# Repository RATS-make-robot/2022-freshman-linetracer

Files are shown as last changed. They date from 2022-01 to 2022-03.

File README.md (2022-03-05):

# 2022-freshman-linetracer

2022 신입생 라인트레이서  

## INTRO
- 신입회원은 가입 후 신입생 세미나(C언어, 라인트레이서 제작)을 거치게 됩니다.   
- 세미나에 적극적으로 참여하고 라인트레이서 완성시, 준회원에서 정회원으로 승급됩니다.  
- 정회원이 되어야 RATS에서 계속 활동할 수 있습니다. 

## 작동 영상
ezgif-1-091fc016d1

## Arduino
  - 아두이노 나노 사용
  - 예제 파일 올려둠
    - LED
    - MOTOR
    - SENSOR
## Modeling
  - `Solidworks 2020`으로 설계
  - `몸체`와 `몸체2`를 3D 프린터로 출력 후 조립

## Reference
  - 사용 부품의 데이터 시트 모음

## Schematic
  - `KiCAD`로 회로도 작성

## 부품리스트

[부품리스트 (가격과 판매처 링크가 포함된 버전)](https://mokhwasomssi.notion.site/bc81dec099644cce938beb7883b7c5f4)
- 소자
    |부품|종류|용도|
    |---|---|---|
    |아두이노 나노 호환보드|MCU|라트 개발보드|  
    |스위치|스위치|라트 전원 스위치|
    |7805|레귤레이터|전원부 레귤레이터|
    |캐패시터 0.33uF|캐패시터|전원부 캐패시터|
    |캐패시터 0.1uF|캐패시터|전원부 캐패시터|
    |저항 330Ω|저항|LED 저항|
    |저항 1MΩ|저항|수광 소자 저항|
    |저항 220Ω|저항|발광 소자 저항|
    |LED|LED|전원부 출력 확인, 센서 값 확인|
    |ST5811|발광 소자|주행선 감지|
    |SI5312-H|수광 소자|주행선 감지|

- 모터, 배터리
  |부품|종류|용도|
  |---|---|---|
  |아두이노 RC카 모터|모터|모터|
  |아두이노 RC카 바퀴|바퀴|바퀴|
  |배터리 18650 1200mAh|배터리|리튬 이온 배터리, 충전 가능|
  |배터리 홀더|배터리|18650x2 홀더|

- 소켓, 커넥터, 점퍼
  |부품|종류|용도|
  |---|---|---|
  |핀헤더|소켓|12핀 : 센서 전원, 신호  </br> 8핀 : 모터 전원, 신호|
  |핀헤더소켓|소켓|30핀 : 아두이노</br>3핀 : 레귤레이터|
  |몰렉스 커넥터 - M|커넥터|전원 커넥터|
  |몰렉스 커넥터 - F|커넥터|전원 커넥터|
  |소켓 점퍼 케이블 - F/F|점퍼|센서 전원 및 신호</br>모터드라이버 신호|
  |소켓 점퍼 케이블 - M/F|점퍼|모터드라이버 전원</br>모터 전선|

- 조립
  |부품|종류|용도|
  |----|---|---|
  |부품 수납 케이스|공구함|개인 부품 보관|
  |만능기판 100X100|만능기판|메인보드 납땜|
  |만능기판 100X50|만능기판|센서보드 납땜|
  |서포트 40mm|서포트|메인보드 서포트|
  |서포트 10mm|서포트|모터드라이버 서포트|
  |볼트 M3x10|볼트|메인보드 서포트 고정</br>모터드라이버 서포트 고정</br>볼캐스터 고정</br>센서보드 고정|
  |볼트 M3x16|볼트|몸체-몸체2 조립|
  |볼트 M3x30|볼트|모터 고정|
  |너트 M3|너트|너트|
  |볼캐스터 5/8|볼캐스터|마찰 방지|
  |십자 드라이버 3mm|드라이버|라트 조립|
    
## NOTE
- 배터리 전선에 몰렉스 커넥터 달아야 함
  - 클램프 필수
- 배터리 홀더에 18650 잘 안들어감
  - 꾸겨넣으세요
- 5V랑 ADC 출력 부분이 플럭스로 이어져있으면 ADC 값이 잘 안 받아짐
  - 이유는 잘 모르겠고 경험적으로

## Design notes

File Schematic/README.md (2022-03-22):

# Schematic


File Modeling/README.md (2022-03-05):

# Modeling 

- 제작할 라인트레이서를 3D 모델링 하였습니다.   
- 3D 프린터로 출력해야하는 파트는 `몸체`와 `몸체2`입니다. 
- 출력 파트의 STL 파일, G-code 파일도 업로드 하였습니다. 





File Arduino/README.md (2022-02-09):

# Arduino

## 아두이노 나노 Upload 세팅


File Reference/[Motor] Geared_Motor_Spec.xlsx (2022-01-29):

MODEL | VOLTAGE |  | NO LOAD |  | AT MAXIMUM EFFICIENCY |  |  |  |  | STALL
 | OPERATING RANGE | NOMINA | SPEED | CURRENT | SPEED | CURRENT | TORQUE |  | OUTPUT | TORQUE |  | CURRENT
 |  | V | r/min | A | r/min | A | N.m | Kg.cm | w | N.m | Kg.cm | A
NP02D-288 | 3.0 - 12.0 | 6 | 21 | 0.1 | 19 | 0.17 | 0.05 | 0.47 | 0.18 | 0.18 | 1.8 | 0.6
MODEL | VOLTAGE |  | NO LOAD |  | AT MAXIMUM EFFICIENCY |  |  |  |  | STALL
 | OPERATING RANGE | NOMINA | SPEED | CURRENT | SPEED | CURRENT | TORQUE |  | OUTPUT | TORQUE |  | CURRENT
 |  | V | r/min | A | r/min | A | N.m | Kg.cm | w | N.m | Kg.cm | A
NP01S-220 | 3.0 - 6.0 | 3 | 50 | 0.25 | 34 | 0.45 | 0.07 | 0.71 | 0.52 | 0.24 | 2.4 | 1.1
MODEL | VOLTAGE |  | NO LOAD |  | AT MAXIMUM EFFICIENCY |  |  |  |  | STALL
 | OPERATING RANGE | NOMINA | SPEED | CURRENT | SPEED | CURRENT | TORQUE |  | OUTPUT | TORQUE |  | CURRENT
 |  | V | r/min | A | r/min | A | N.m | Kg.cm | w | N.m | Kg.cm | A
NP01D-48 | 3.0 - 9.0 | 3 | 110 | 0.12 | 85 | 0.2 | 0.01 | 0.11 | 0.13 | 0.027 | 0.27 | 1.45

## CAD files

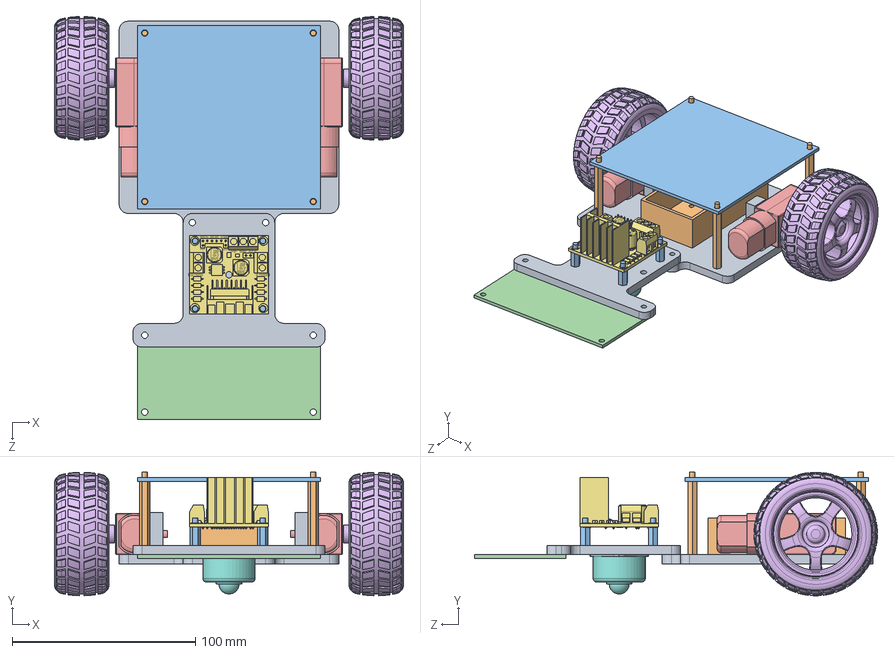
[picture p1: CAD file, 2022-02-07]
Modeling/Modeling Files/조립.SLDASM
190.8 x 67.5 x 220.0 mm
몸체
배터리홀더
메인보드 100x100
센서보드 50x100
모터 x 2
바퀴 x 2
모터드라이버
볼캐스터
몸체2
서포트 M3x40 x 4
서포트 M3x10 x 4

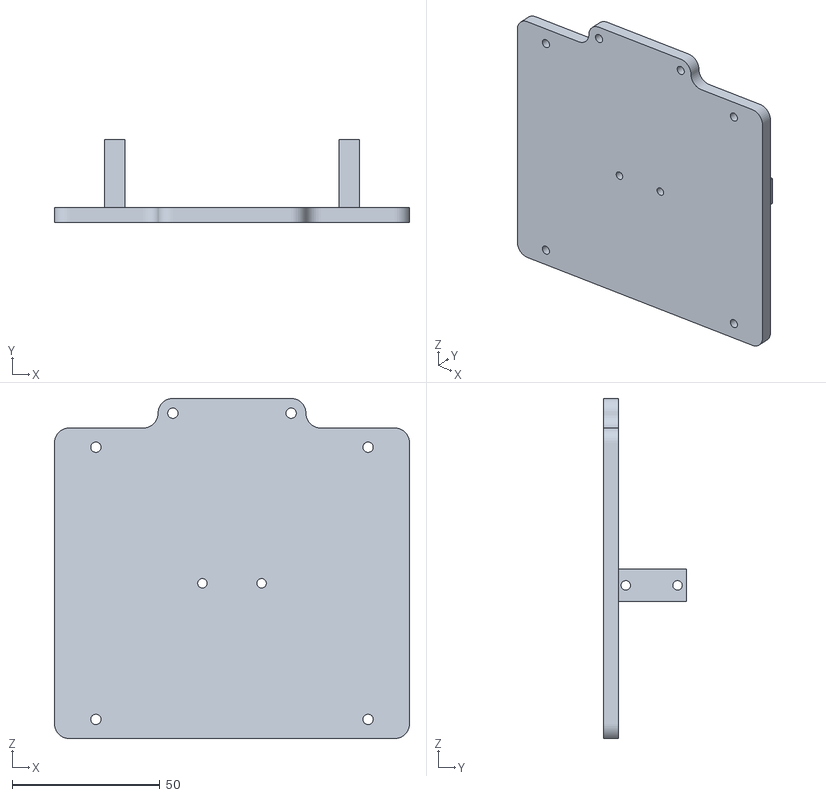
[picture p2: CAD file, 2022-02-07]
Modeling/[출력] 몸체.STL
120.0 x 28.0 x 115.0

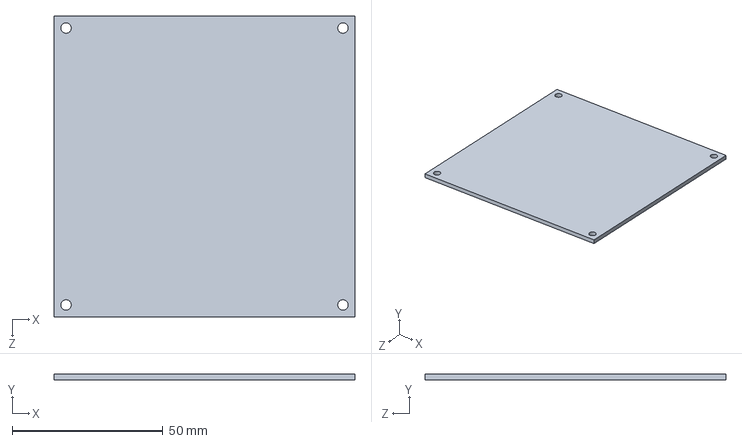
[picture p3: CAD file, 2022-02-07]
Modeling/Modeling Files/메인보드 100x100.SLDPRT
100.0 x 2.00 x 100.0 mm

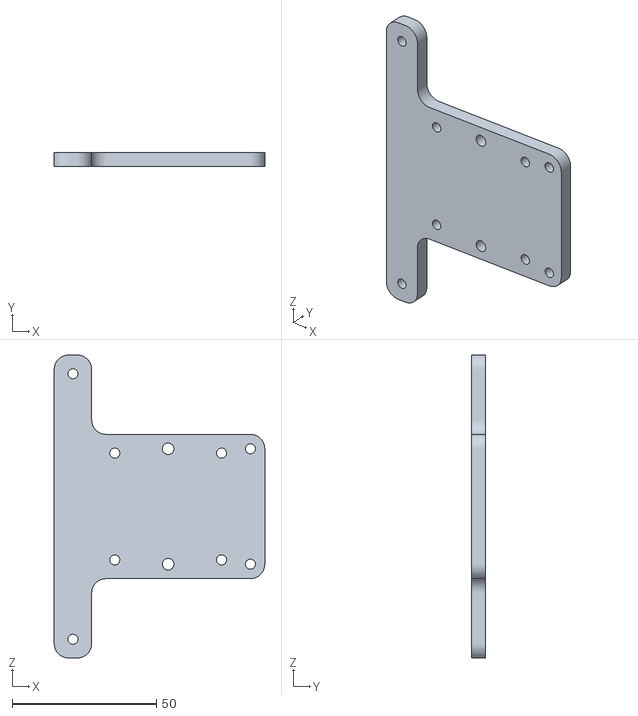
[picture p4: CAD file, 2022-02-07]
Modeling/[출력] 몸체2.STL
73.0 x 5.00 x 105.0

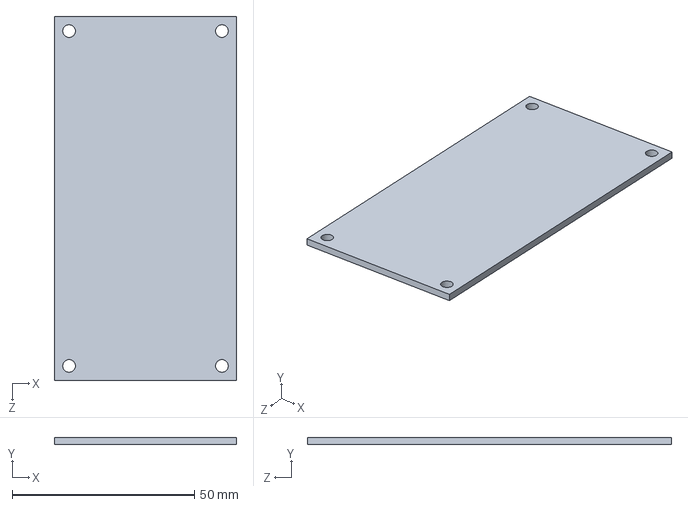
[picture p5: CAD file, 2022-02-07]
Modeling/Modeling Files/센서보드 50x100.SLDPRT
50.0 x 2.00 x 100.0 mm

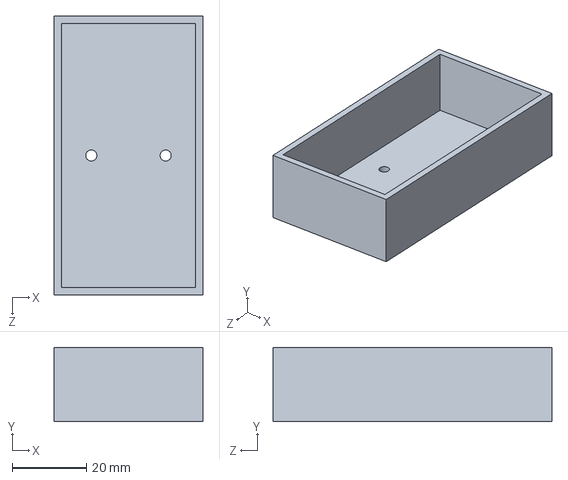
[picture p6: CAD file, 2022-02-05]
Modeling/Modeling Files/배터리홀더.SLDPRT
40.0 x 20.0 x 75.0 mm

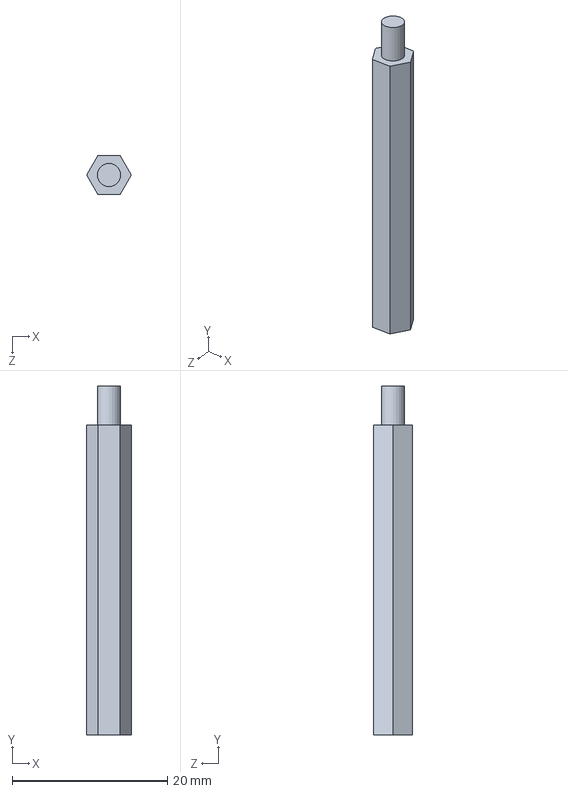
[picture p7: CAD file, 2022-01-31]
Modeling/Modeling Files/서포트 M3x40.SLDPRT
5.77 x 45.0 x 5.00 mm

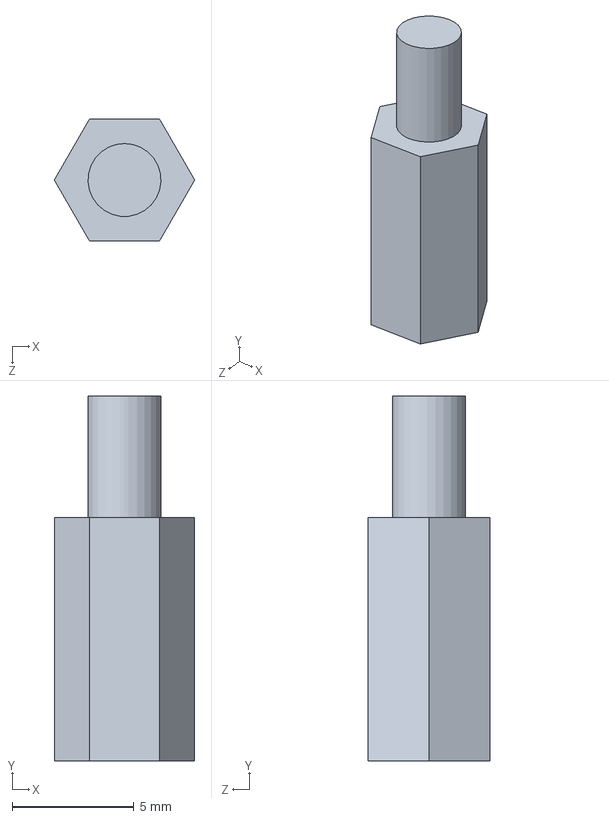
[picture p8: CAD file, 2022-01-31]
Modeling/Modeling Files/서포트 M3x10.SLDPRT
5.77 x 15.0 x 5.00 mm

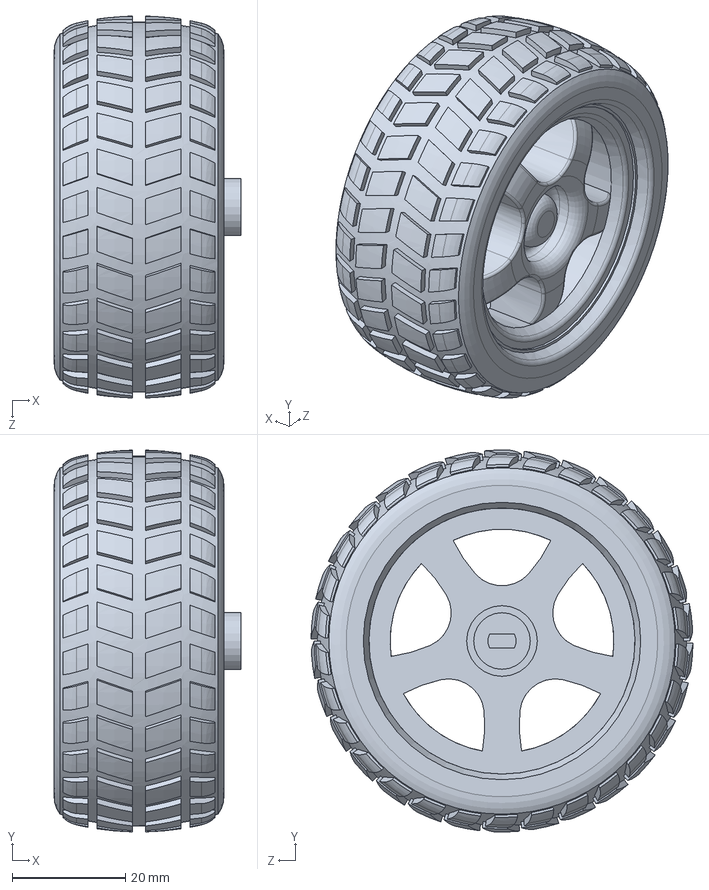
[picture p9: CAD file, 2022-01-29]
Modeling/Modeling Files/바퀴.SLDPRT
33.0 x 67.4 x 67.5 mm

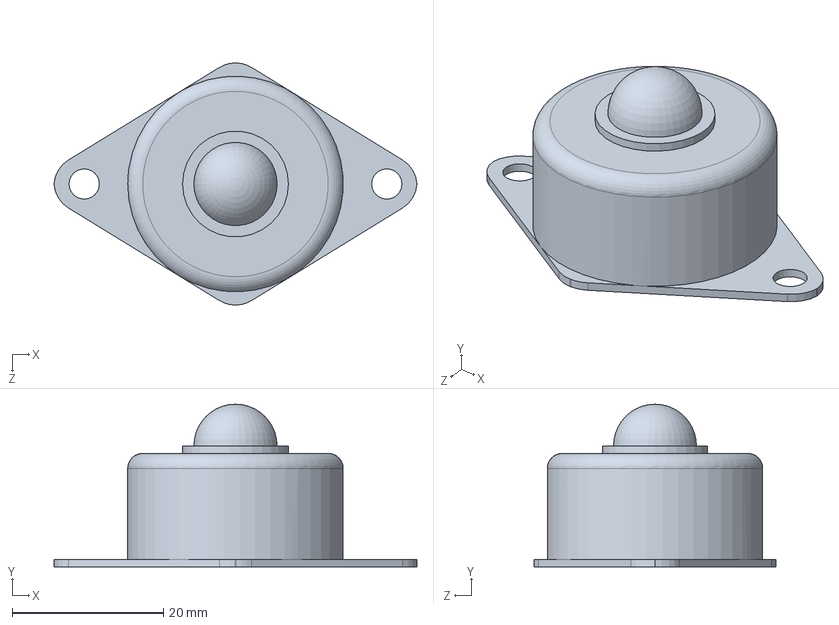
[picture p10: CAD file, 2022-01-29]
Modeling/Modeling Files/볼캐스터.SLDPRT
48.0 x 21.5 x 32.0 mm

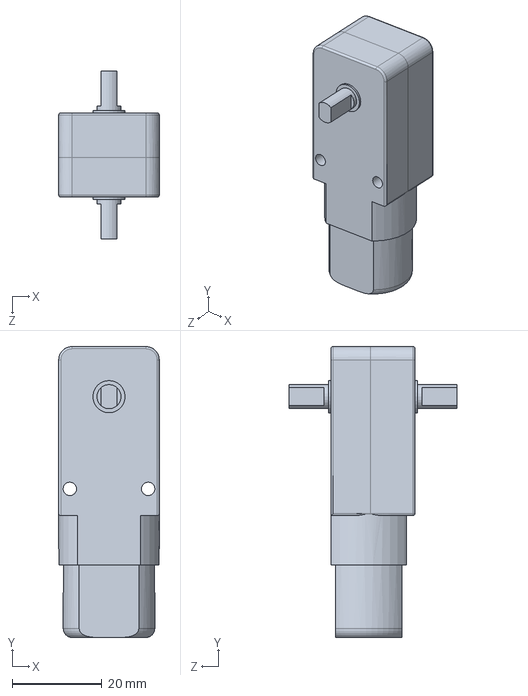
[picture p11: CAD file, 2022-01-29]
Modeling/Modeling Files/모터.SLDPRT
22.5 x 65.0 x 37.6 mm

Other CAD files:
Modeling/Modeling Files/몸체.SLDPRT
Modeling/Modeling Files/몸체2.SLDPRT

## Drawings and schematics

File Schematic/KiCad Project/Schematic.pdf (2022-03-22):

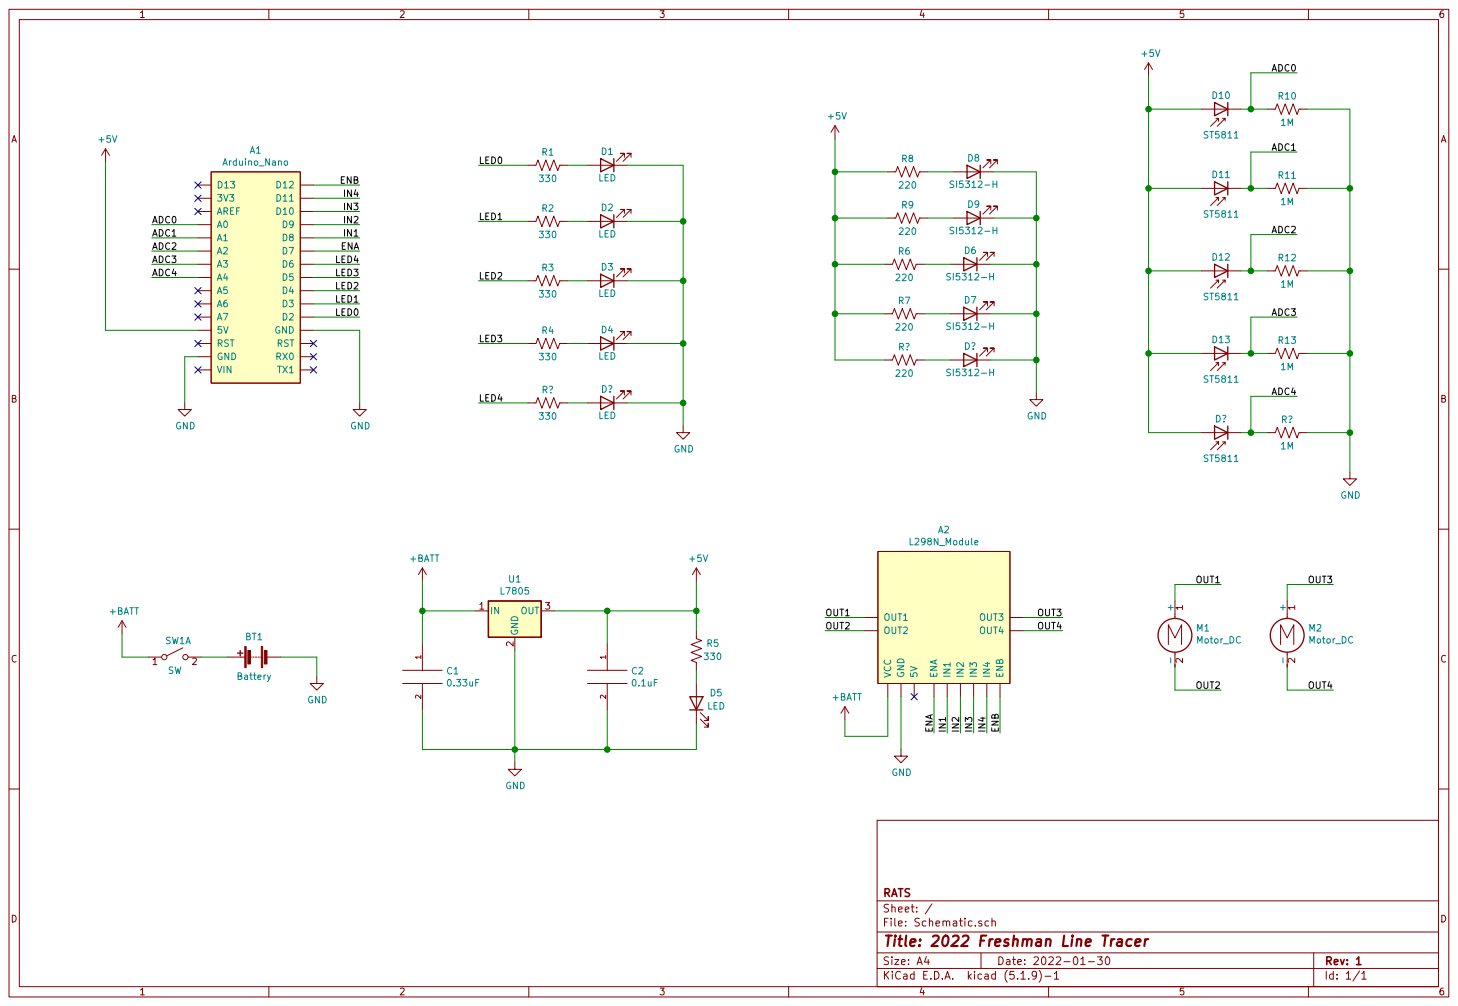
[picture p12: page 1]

Id: 1/1 Title: 2022 Freshman Line Tracer File: Schematic.sch Sheet: / RATS

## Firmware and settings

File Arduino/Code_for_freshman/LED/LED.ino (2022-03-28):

#define LED_0 6
#define LED_1 5
#define LED_2 4
#define LED_3 3
#define LED_4 2

void setup() {
  pinMode(LED_0, OUTPUT);
  pinMode(LED_1, OUTPUT);
  pinMode(LED_2, OUTPUT);
  pinMode(LED_3, OUTPUT);
  pinMode(LED_4, OUTPUT);
  
  digitalWrite(LED_0, LOW);
  digitalWrite(LED_1, LOW);
  digitalWrite(LED_2, LOW);
  digitalWrite(LED_3, LOW);
  digitalWrite(LED_4, LOW);
}

void loop() {
  digitalWrite(LED_4, LOW);
  digitalWrite(LED_0, HIGH);
  delay(500);
  digitalWrite(LED_0, LOW);
  digitalWrite(LED_1, HIGH);
  delay(500);
  digitalWrite(LED_1, LOW);
  digitalWrite(LED_2, HIGH);
  delay(500);
  digitalWrite(LED_2, LOW);
  digitalWrite(LED_3, HIGH);
  delay(500);
  digitalWrite(LED_3, LOW);
  digitalWrite(LED_4, HIGH);
  delay(500);
}

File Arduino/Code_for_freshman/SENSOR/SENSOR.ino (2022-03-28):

#define SENSOR_0 A0
#define SENSOR_1 A1
#define SENSOR_2 A2
#define SENSOR_3 A3
#define SENSOR_4 A4

int sensor_value0 = 0;
int sensor_value1 = 0;
int sensor_value2 = 0;
int sensor_value3 = 0;
int sensor_value4 = 0;

void setup() {
  Serial.begin(9600);
}

void loop() {
  sensor_value0 = analogRead(SENSOR_0);
  sensor_value1 = analogRead(SENSOR_1);
  sensor_value2 = analogRead(SENSOR_2);
  sensor_value3 = analogRead(SENSOR_3);
  sensor_value4 = analogRead(SENSOR_4);

  Serial.print(sensor_value0);
  Serial.print("\t");
  Serial.print(sensor_value1);
  Serial.print("\t");
  Serial.print(sensor_value2);
  Serial.print("\t");
  Serial.print(sensor_value3);
  Serial.println("\t");
  Serial.print(sensor_value4);
  Serial.println("\t");
}

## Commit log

2022-01-29 Add Modeling Folder
    - 주요 부품 배치 완료
    - 만능기판, 모터드라이브 실측 후 마운팅 홀 타공
    [메인부 100x100.SLDPRT, 모터.SLDPRT, 몸체.SLDPRT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]
2022-01-29 Update Reference
    - 노란모터사양 엑셀 파일 추가
    [노란모터사양.xlsx]
2022-01-30 Add Schmatic
    - 각 소자 저항 값은 아직 안넣음
    [Schematic.kicad_pcb, Schematic.sch]
2022-01-30 Update Schematic
    - Rename Global Label
    [Schematic.sch]
2022-01-30 Update Schematic
    - Add resistor values
    [Schematic.sch]
2022-01-30 Update Reference
    [[Motor] Geared_Motor_Spec.xlsx]
2022-01-31 Update Modeling
    - 서포트 추가
    [메인부 100x100.SLDPRT, 몸체.SLDPRT, 몸체2.SLDPRT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]
2022-01-31 Update README.md
    - 3d 모델링 사진 교체
2022-02-02 Update Schematic
    - 전원부 회로 추가
    - LED 저항 330옴으로 변경
    [Schematic.sch]
2022-02-02 Update Reference
    - L7805 데이터시트 추가
2022-02-02 Update Schematic
    - 스위치 위치 수정
    [Schematic.sch]
2022-02-05 Update Modeling
    - 모터 고정 부분 수정
    [메인보드 100x100.SLDPRT, 메인부 100x100.SLDPRT, 몸체.SLDPRT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]
2022-02-05 Update Modeling
    - 배터리 홀더 제품 변경
    - 몸체에 배터리 홀더 고정 홀 뚫음
    [몸체.SLDPRT, 배터리홀더.SLDPRT, 조립.SLDASM]
2022-02-07 Update Modeling
    - 만능기판 홀 치수 수정 : 3.75->4.00
    - 3D 프린터 출력 모델 STL 파일 추가
    - G-code 생성
    - Snapmaker 파일도 저장
    [[출력] 몸체.STL, [출력] 몸체2.STL, 메인보드 100x100.SLDPRT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]
2022-02-07 Update Schematic
    - global label에서 net label로 수정
    [Schematic.sch]
2022-02-07 Update README.md
    - 회로소 사진 업데이트
2022-02-09 Add Arduino folder
    - 아두이노 스케치 파일 저장소
2022-02-09 Update Arduino
    - LED 예제 추가
2022-02-09 Update Arduino
    - MOTOR 예제 추가
    - SENSOR 예제 추가
2022-02-09 Update Modeling
    - 더 작은 볼캐스토로 교체
    - 몸체, 몸체2 -> 베이스로 변경
    - 3d 프린터 출력물 하나로 줄임
    [[출력] 몸체.STL, [출력] 몸체2.STL, 몸체.SLDPRT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]
2022-02-09 Update Modeling
    - 모델링 폴더에 리드미 추가
    [메인보드 100x100.SLDPRT, 모터.SLDPRT, 바퀴.SLDPRT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]
2022-02-09 Update Schematic
    - 수발광 종류 변경
    [Schematic.kicad_pcb, Schematic.sch]
2022-02-09 Update Schematic
    - 카이캐드 프로젝트 파일 분리
    - 리드미 생성
2022-02-10 Update Modeling
    - 베이스 파트 디자인 변경
    [베이스.SLDPRT, 베이스.STL, 조립.SLDASM]
2022-02-21 Update Modeling
    - 소형 볼캐스터 물량이 없음
    - 기존 설계로 복귀 (몸체, 몸체2 조립)
    - 커밋 a420936 상태의 Modeling 폴더 복붙
    [[출력] 몸체.STL, [출력] 몸체2.STL, 메인보드 100x100.SLDPRT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]
2022-02-21 Update README.md
    - 부품리스트 표 추가
2022-02-21 Update README.md
    - 작동영상(gif) 추가
2022-03-05 Update Modeling
    - 순수 모델링 파일 폴더로 묶음
    - 모델링 리드미 추가
    [메인보드 100x100.SLDPRT, 모터.SLDPRT, 몸체.SLDPRT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]
2022-03-05 Update README.md
    - 노션으로 정리한 부품리스트 추가
    - 가격과 판매처 정보가 포함되어있음
2022-03-22 센서 5조 수정
    [Schematic.sch]
2022-03-22 Scim readme 반영
